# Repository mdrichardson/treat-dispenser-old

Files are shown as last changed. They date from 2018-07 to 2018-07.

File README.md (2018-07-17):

# Treat Dispenser and Web App

This is a dog treat dispenser that dispenses treats based off of input from a progressive web app, time intervals, and or feeding schedule. The dispenser, itself, is based loosely off of [this model.](https://www.thingiverse.com/thing:27854)

**Note: This previously used [Auth0](http://www.auth0.com) for user authentication and metadata storage. Since re-uploading this app, Auth0 deprecated the authorization process used and quite a bit of work is required to get it back. On the current live site, this uses Basic Authentication. Some of the old Auth0 code is still in `app.js` for easier transitioning into the up-to-date auth process.**

## TreatDispenser.ino

This is the code executed on a Particle Photon (similar to an Arduino--uses C/C++).

### Features

* Dispense treat on command
* Dispense treat on customizable intervals
* Dispense treat on customizable schedule
* Dispense treats or meals in customizable sizes/amounts
* Optionally play an audible "warning tone" of customizable frequency before dispensing
  * When I first used this, my dog was scared of the sound of the servo. Adding the "warning" tone helped
* Track how often your dog barks so that you can not dispense a treat if they are barking too much
  * You need something else to track the barks and send the command to the Photon. I used a webcam that executed a bark tracking script on my PC
* All settings can be tracked and changed in a web app

### How it Works

1. Command for dispensing treat is sent to Photon based off of user input, interval, or schedule
2. Photon receives command over its Wi-Fi connection
3. Photon optionally plays "warning" tone so dog isn't scared of servo starting up
4. Photon spins servo (motor) to push treats out of the dispensing hole
    * The amount it spins is time-based and can be customized
5. Dispensing is complete and web app is notified

### Hardware

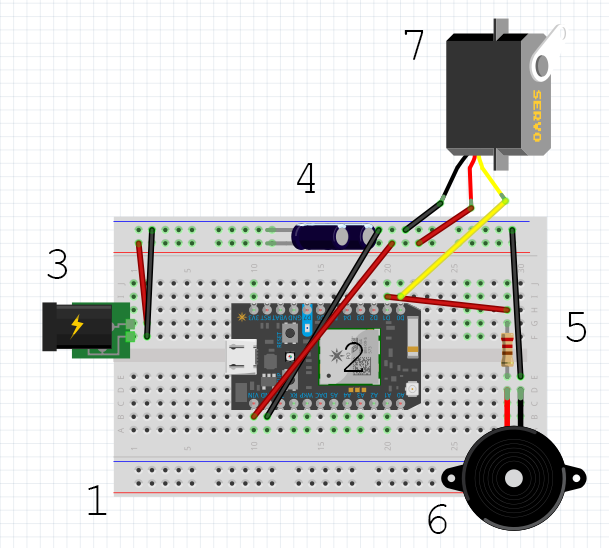
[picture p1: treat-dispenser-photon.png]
Particle Photon Treat Dispenser


1. Breadboard - Connects all of the hardware pieces together
2. Particle Photon - Executes all code
3. Power Adapter - Additional power had to be applied because I used a servo with greater-than-standard torque. Otherwise, the Photon can be powered via USB
4. Capacitors - Provides cleaner power to the servo and helps prevent mechanical bugs
5. Resistor - Decreases power sent to speaker, so the "warning" tone is quieter
6. Piezo Speaker - Plays "warning" tone
7. Servo - Turns the auger, which dispenses treats

## public (folder)

This is the progressive web app. See the [`README.md`](https://github.com/mdrichardson/treat-dispenser/blob/master/public/README.md) inside it for details

## auger*.stl

These are the 3D-printed parts for the auger, which is used to dispense the treats.

## Limitations

* Currently only works with small treats
  * This can be fixed by using a larger auger
* Treats can easily become jammed or not dispense at all
  * A gravity-fed system would work better than this, which pushes horizontally
* Particle Photon has limited memory, which decreases:
  * Number of web variables - It would be nice to be able to track more.
    * I mostly overcame this limitation by rolling multiple variables into single `char` pointers
  * Number of features - More efficient code might allow for more
* Photon variables reset to defaults on power reset
  * This can be mitigated by storing them in the web database and having the Photon request them on startup

## To-Do

- [X] Comment the web app code
- [X] Host the web app again -- I took it down and deleted Auth0 account after no longer using it
- [ ] Re-write Photon code -- [They updated their JS API to use OOP](https://docs.particle.io/reference/javascript/#installation)
- [ ] Re-write the app in Angular -- Removing [Auth0](http://www.auth0.com) makes a re-write pretty much necessary anyway
- [ ] Replace basic authentication with own user authentication database -- I removed authentication because auth0 no longer supports the legacy auth0 authentication the app *was* using
- [ ] Simplify the Photon code. Scheduling features aren't really necessary.

## Needs to be done, but won't be unless I pick the project back up

- [ ] 3D print a gravity-fed system
- [ ] Store variable values in web database and have Photon request them at startup

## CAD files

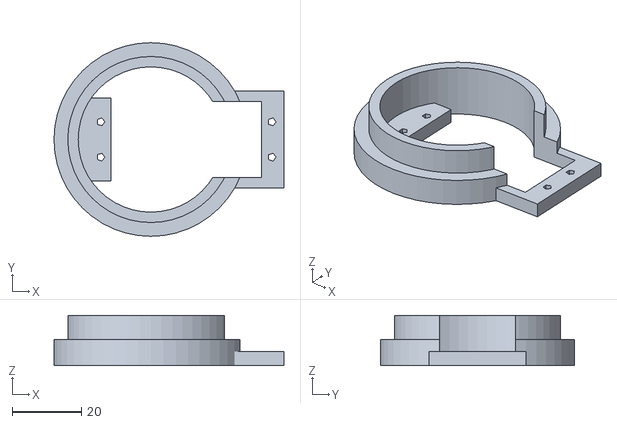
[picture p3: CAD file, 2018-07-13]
auger_tubemount.stl
66.5 x 56.0 x 14.5

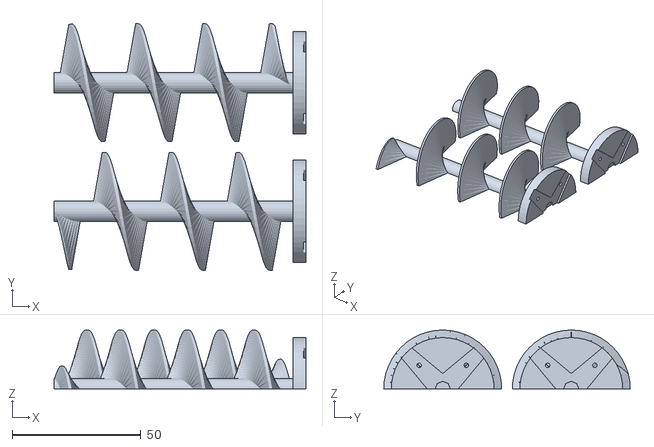
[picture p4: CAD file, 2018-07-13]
auger_screwplate.stl
98.0 x 95.9 x 22.9

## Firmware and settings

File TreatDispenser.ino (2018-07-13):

// This #include statement was automatically added by the Particle IDE.
#include <SparkTime.h>

/*##################################################
#
#
#                Treat Dispenser
#        MAX 20 VARIABLES, 15 FUNCTIONS
#
###################################################*/

/*##################################################
#
#                  Servo
#
##################################################*/
Servo myservo;// create servo object using the built-in Particle Servo Library
int servoPin = D0;  //declare variable for servo
int run = 0; //for stopping a continuous push/pull

int stop = 1500;
int push = 0;
int pull = 180;
int pullDelay = 600;
int maxDelay = 3000;
int loadDelay = 7500;

unsigned long lastTime = 0UL;

String last = "?"; //declare variable for time since last action

/*##################################################
#
#                  Time Zone
#
##################################################*/
int tZone = -8; // Default is PST
UDP UDPClient;
SparkTime rtc;

/*##################################################
#
#                  Interval Dispensing
#
##################################################*/
int intervalOn = 0;
int intervalSEon = 1;
int intervalStart = 800;
int intervalEnd = 1700;
int intMinutes = 30;
int intHours = 1;
int intImmediate = 1;
int intervalFirst = 1;

char intervals[256];
// send the interval values in json format
char *getIntervals()
{
    sprintf(intervals,"{\"on\": %d, \"SE\": %d, \"start\": %d, \"end\": %d, \"min\": %d, \"hr\": %d, \"imm\": %d}"
    ,intervalOn,intervalSEon,intervalStart,intervalEnd,intMinutes,intHours,intImmediate);
    return intervals;
}

unsigned long lastInt = 0UL;

/*##################################################
#
#                  Scheduled Dispensing
#
##################################################*/
int scheduleOn = 0;
int schedTime1On = 0;
int schedTime2On = 0;
int schedTime3On = 0;
int schedTime1S = 1;
int schedTime2S = 1;
int schedTime3S = 1;
int schedTime1 = 800;
int schedTime2 = 1200;
int schedTime3 = 1700;
int schedSun = 0;
int schedMon = 0;
int schedTue = 0;
int schedWed = 0;
int schedThu = 0;
int schedFri = 0;
int schedSat = 0;

char scheduleInfo[256];
// send the schedule values in json format
char *getSchedInfo()
{
    sprintf(scheduleInfo,"{\"on\": %d, \"t1on\": %d, \"t2on\": %d, \"t3on\": %d, \"t1s\": %d, \"t2s\": %d, \"t3s\": %d, \"t1\": %d, \"t2\": %d, \"t3\": %d}",scheduleOn,schedTime1On,schedTime2On,schedTime3On,schedTime1S,schedTime2S,schedTime3S,schedTime1,schedTime2,schedTime3);
    return scheduleInfo;
}

char scheduleDays[256];
// send the schedule day values in json format
char *getSchedDays()
{
    sprintf(scheduleDays,"{\"sun\": %d, \"mon\": %d, \"tue\": %d, \"wed\": %d, \"thu\": %d, \"fri\": %d, \"sat\": %d}",schedSun,schedMon,schedTue,schedWed,schedThu,schedFri,schedSat);
    return scheduleDays;
}

unsigned long lastSchedule = 0UL;

/*##################################################
#
#                  Dispensing Amounts
#
##################################################*/
int treatSize = 0; //0=S,1=M,2=L
int mealSize = 0;

char sizes[256];
// send the size values in json format
char *getSizes()
{
    sprintf(sizes,"{\"treat\": %d, \"meal\": %d}",treatSize,mealSize);
    return sizes;
}

int treatDelay = 1500;
int mealDelay = 20000;
int treatDispense;
int mealDispense;

/*##################################################
#
#                  Dispense Warning Tone
#
##################################################*/
int tonePin = D1;
int toneDuration = 100;
int toneDelay = 750;
int tone1 = 1568; // Frequency for G6 tone
int tone2 = 2093; // Frequency for G3 tone
int servingDelay = 750;
int useTone = 1;

/*##################################################
#
#                  Debugging Support
#
##################################################*/
char debugServo[256];
// send the debug values in json format
char *getDebugServo()
{
    sprintf(debugServo,"{\"stop\": %d, \"push\": %d, \"pull\": %d, \"pullD\": %d, \"maxD\": %d, \"loadD\": %d, \"treatD\": %d, \"mealD\": %d}"
    ,stop,push,pull,pullDelay,maxDelay,loadDelay,treatDelay,mealDelay);
    return debugServo;
}
char debugTone[256];
// send the tone values in json format
char *getDebugTone()
{
    sprintf(debugTone,"{\"duration\": %d, \"toneD\": %d, \"tone1\": %d, \"tone2\": %d, \"servingD\": %d, \"use\": %d}"
    ,toneDuration,toneDelay,tone1,tone2,servingDelay,useTone);
    return debugTone;
}

String OGdebugServo = "{\"stop\": "+String(stop)+", \"push\": "+String(push)+", \"pull\": "+String(pull)+
    ", \"pullD\": "+String(pullDelay)+", \"maxD\": "+String(maxDelay)+", \"loadD\": "+String(loadDelay)+", \"treatD\": "+
    String(treatDelay)+", \"mealD\": "+String(mealDelay)+"}";
    
String OGdebugTone = "{\"duration\": "+String(toneDuration)+", \"toneD\": "+String(toneDelay)+", \"tone1\": "+String(tone1)+
    ", \"tone2\": "+String(tone2)+", \"servingD\": "+String(servingDelay)+", \"use\": "+String(useTone)+"}";

/*##################################################
#
#                  Track Barks
#
##################################################*/    
int barkCount = 0;
int lastBark = 0UL;
/*##################################################
#
#                  Servo Setup
#
##################################################*/
void setup()
{
    myservo.attach(servoPin); // Initialize the servo attached to pin D0
    myservo.detach(); //detach the servo to prevent it from jittering

/*##################################################
#
#                  Declare Cloud Functions
#
##################################################*/
    Particle.function("setTimeZone",setTimeZone);
    Particle.function("auger",auger);
    Particle.function("setInterval",setInterval);
    Particle.function("setSchedule",setSchedule);
    Particle.function("setSizes",setSizes);
    Particle.function("test",test);
    Particle.function("debug",setDebug);
    Particle.function("bark",bark);
    
/*##################################################
#
#                  Declare Cloud Variables
#
##################################################*/
    Particle.variable("connected","yes");
    Particle.variable("tZone",tZone);
    Particle.variable("intervals",getIntervals());
    Particle.variable("scheduleInfo",getSchedInfo());
    Particle.variable("scheduleDays",getSchedDays());
    Particle.variable("sizes",getSizes());
    Particle.variable("debugServo",getDebugServo());
    Particle.variable("debugTone",getDebugTone());
    Particle.variable("OGdebugServo",OGdebugServo);
    Particle.variable("OGdebugTone",OGdebugTone);
    Particle.variable("last", last);
    Particle.variable("barkCount",barkCount);
    Particle.variable("lastBark",lastBark);

 /*##################################################
#
#                  Startup Notifications
#
##################################################*/ 
    Particle.publish("activity", "Starting");
    Particle.publish("status", "Connected");
    Particle.publish("command","update"); // Ensure that page is updated if device reboots
    
    
    
 /*##################################################
#
#                  Time Zone Setup
#
##################################################*/
    rtc.begin(&UDPClient, "north-america.pool.ntp.org");
    rtc.setTimeZone(tZone);
    rtc.setUseDST(true);
        
}
 /*##################################################
#
#                  Looping Functions
#
##################################################*/
void loop()
{
    // Every 10 seconds publish connection status
    unsigned long now = millis();
    if (now-lastTime>10000UL)
    {
        lastTime = now;
        Particle.publish("status", "Connected");
    }
    // Check if interval needs to run
    if (intervalOn == 1)
    {
        unsigned long intervalInt = (intMinutes * 60000) + (intHours * 360000);
        if (intImmediate == 1 && intervalFirst == 1)
        {
            intervalFirst = 0;
            treats();
            lastInt = now;
            Particle.publish("Interval","Dispensing");
        }
        if (now - lastInt > intervalInt)
        {
            treats();
            lastInt = now;
            Particle.publish("Interval","Dispensing");
        }
    }
    // Check if Schedule needs to run
    if (scheduleOn == 1)
    {
        unsigned long currentDay = Time.weekday(Time.now());
        if ((schedSun == 1 && currentDay == 1) || (schedMon == 1 && currentDay == 2) || (schedTue == 1 && currentDay == 3) || (schedWed == 1 && currentDay == 4) || (schedThu == 1 && currentDay == 5)
         || (schedFri == 1 && currentDay == 6) || (schedSat == 1 && currentDay == 7))
         {
            String currentTime = rtc.hourString(rtc.now()) + rtc.minuteString(rtc.now());
            int currentTimeInt = atoi(currentTime);
            if (currentTimeInt == schedTime1 || currentTimeInt == schedTime2 || currentTimeInt == schedTime3)
            {
                if (now-lastSchedule > 5 * 60000UL) // Ensure there's at least a 5 minute delay between dispensing
                {
                    lastSchedule = now;
                    if (currentTimeInt == schedTime1)
                    {
                        if (schedTime1S == 0)
                        {
                            treats();
                            Particle.publish("Schedule","Dispensing Treat");
                        } else {
                            meals();
                            Particle.publish("Schedule","Dispensing Meal");
                        }
                    } else if (currentTimeInt == schedTime2) {
                        if (schedTime2S == 0)
                        {
                            treats();
                            Particle.publish("Schedule","Dispensing Treat");
                        } else {
                            meals();
                            Particle.publish("Schedule","Dispensing Meal");
                        }
                    } else if (currentTimeInt == schedTime3) {
                        if (schedTime3S == 0)
                        {
                            treats();
                            Particle.publish("Schedule","Dispensing Treat");
                        } else {
                            meals();
                            Particle.publish("Schedule","Dispensing Meal");
                        }
                    }
                    
                }
            }
         }
    }
}

 /*##################################################
#
#                  Time Zone Functions
#
##################################################*/
int setTimeZone(String offset)
{
    tZone = atoi(offset);
    rtc.setTimeZone(tZone);
    return 1;
}

 /*##################################################
#
#                  Tone Functions
#
##################################################*/
void playTone()
{
    if (useTone == 1)
    {
        tone(tonePin, tone1, toneDuration);
        delay(toneDelay + toneDuration);
        tone(tonePin, tone2, toneDuration);
        delay(servingDelay + toneDuration);
    }
}

 /*##################################################
#
#                  Servo functions
#
##################################################*/
// stop the servo
void end()
{
    run = 0;
    myservo.writeMicroseconds(stop);
    delay(1000);
    Particle.publish("activity", "Idle");
}

// dispense treats
void treats()
{
    if (treatSize == 0)
    {
        treatDispense = treatDelay;
    }
    else if (treatSize == 1)
    {
        treatDispense = treatDelay * 1.5;
    }
    else if (treatSize == 2)
    {
        treatDispense = treatDelay * 2;
    }
    noJam(treatDispense);
}

// dispense meals
void meals()
{
    if (mealSize == 0)
    {
        mealDispense = mealDelay;
    }
    else if (mealSize == 1)
    {
        mealDispense = mealDelay * 1.5;
    }
    else if (mealSize == 2)
    {
        mealDispense = mealDelay * 2;
    }
    noJam(mealDispense);
}

// briefly reverse auger and push again to prevent jams
void noJam(int amount)
{
    int remaining = amount;
    run = 1;
    Particle.publish("activity", "Dispensing");
    myservo.attach(servoPin);
    playTone();
    while (remaining > 0)
        {
        if (remaining <= maxDelay)
        {
            myservo.write(push);
            delay(remaining);
            myservo.write(pull);
            delay(pullDelay);
            remaining -= mealDispense;
            break;
        }
        else 
        {
            myservo.write(push);
            delay(maxDelay);
            myservo.write(pull);
            delay(pullDelay);
            remaining -= maxDelay;
        }
    }
    end();
}

// [Web command] move the auger
int auger(String command)
{
    // make sure auger isn't disabled
    if (run == 1)
    {
        end();    
    }
    // Normal commands
    if (command == "load")
    {
        Particle.publish("activity", "Loading");
        noJam(loadDelay);
        return 1;
    }
    else if (command == "treat")
    {
        
        treats();
        last = Time.now();
        return 1;
    }
    else if (command == "meal")
    {
        
        meals();
        last = Time.now();
        return 1;
    }
    // Debugging commands
    else if (command == "out")
    {
        run = 1;
        myservo.attach(servoPin);
        Particle.publish("activity", "Pushing");
        do
            {
                myservo.write(push);
                delay(maxDelay);
                myservo.writeMicroseconds(stop);
                delay(2000);
            } while (run==1);
        return 1;
    }
    else if (command == "in")
    {
        run = 1;
        myservo.attach(servoPin);
        Particle.publish("activity", "Pulling");
        do
            {
                myservo.write(pull);
                delay(maxDelay);
                myservo.writeMicroseconds(stop);
                delay(2000);
            } while (run == 1);
        return 1;
    }
    else if (command=="inout")
    {
        run = 1;
        myservo.attach(servoPin);
        do
            {   myservo.write(push);
                delay(maxDelay);
                myservo.write(pull);
                delay(maxDelay);
            } while (run == 1);
        return 1;
    }
    else if (command == "stop")
    {
        end();
        return 1;
    }
    else
    {
        return 0;
    }
    run = 0;
    return 1;
}

// [Web command] set treat sizes
int setSizes(String type0size)
{
    String type;
    String size;
    // Size comes in as a string with variables separated by commas
    // This converts the strings into appropriate variables
    for (int i = 0; i < type0size.length(); i++) {
      if (type0size.substring(i, i+1) == ",") {
        type = type0size.substring(0, i);
        size = atoi(type0size.substring(i+1));
        break;
      }
    }
    if (type == "treat")
    {
        treatSize = atoi(size);
    }
    else if (type == "meal")
    {
        mealSize = atoi(size);
    }
    else
    {
        return -1;
    }
    getSizes();
    return 1;
}

 /*##################################################
#
#                  Interval Functions
#
##################################################*/
// [Web command] Set the interval settings
int setInterval(String command0setting)
{
    String command;
    String setting;
    // command and setting comes in as a string with variables separated by commas
    // This converts the strings into appropriate variables
    for (int i = 0; i < command0setting.length(); i++) {
      if (command0setting.substring(i, i+1) == ",") {
        command = command0setting.substring(0, i);
        setting = atoi(command0setting.substring(i+1));
        break;
      }
    }
    if (command == "on")
    {
        intervalOn = atoi(setting);
        if (setting == "1")
        {
            Particle.publish("Interval","on");
        }
        else
        {
            Particle.publish("Interval","off");
        }
    }
    else if (command == "SEon")
    {
        intervalSEon = atoi(setting);
    }
    else if (command == "start")
    {
        intervalStart = atoi(setting);
    }
    else if (command == "end")
    {
        intervalEnd = atoi(setting);
    }
    else if (command == "minutes")
    {
        intMinutes = atoi(setting);
    }
    else if (command == "hours")
    {
        intHours = atoi(setting);
    }
    else if (command == "immediate")
    {
        intImmediate = atoi(setting);
    }
    else
    {
        return -1;
    }
    getIntervals();
    return 1;
}

 /*##################################################
#
#                  Schedule Functions
#
##################################################*/
// [Web command] Set schedule settings
int setSchedule(String command0setting)
{
    String command;
    String setting;
    // command and setting comes in as a string with variables separated by commas
    // This converts the strings into appropriate variables
    for (int i = 0; i < command0setting.length(); i++) {
      if (command0setting.substring(i, i+1) == ",") {
        command = command0setting.substring(0, i);
        setting = atoi(command0setting.substring(i+1));
        break;
      }
    }
    if (command == "on")
    {
        scheduleOn = atoi(setting);
        if (setting == "1")
        {
            Particle.publish("Schedule","on");
        }
        else
        {
            Particle.publish("Schedule","off");
        }
    }
    else if (command == "t1on")
    {
        schedTime1On = atoi(setting);
    }
    else if (command == "t2on")
    {
        schedTime2On = atoi(setting);
    }
    else if (command == "t3on")
    {
        schedTime3On = atoi(setting);
    }
     else if (command == "t1size")
    {
        schedTime1S = atoi(setting);
    }
    else if (command == "t2size")
    {
        schedTime2S = atoi(setting);
    }
    else if (command == "t3size")
    {
        schedTime3S = atoi(setting);
    }
    else if (command == "t1")
    {
        schedTime1 = atoi(setting);
    }
    else if (command == "t2")
    {
        schedTime2 = atoi(setting);
    }
    else if (command == "t3")
    {
        schedTime3 = atoi(setting);
    }
    else if (command == "sun")
    {
        schedSun = atoi(setting);
    }
    else if (command == "mon")
    {
        schedMon = atoi(setting);
    }
    else if (command == "tue")
    {
        schedTue = atoi(setting);
    }
    else if (command == "wed")
    {
        schedWed = atoi(setting);
    }
    else if (command == "thu")
    {
        schedThu = atoi(setting);
    }
    else if (command == "fri")
    {
        schedFri = atoi(setting);
    }
    else if (command == "sat")
    {
        schedSat = atoi(setting);
    }
    else
    {
        return -1;
    }
    getSchedInfo();
    getSchedDays();
    return 1;
}
 /*##################################################
#
#                  Debugging Functions
#
##################################################*/
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
